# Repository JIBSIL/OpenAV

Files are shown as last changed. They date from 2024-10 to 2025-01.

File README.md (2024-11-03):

## OpenAV

### Important Note

OpenAV is still in beta! Please review the schematic, BOM and PCB to adjust the OpenAV kit to your requirements. It is untested so far, so it may have major bugs and other issues.

### Information
The OpenAV PCB was created to be a universal system for rocketry - with a LoRa long distance radio, a SIM800C for geolocation and Internet communication, an ESP32 for WiFi support and an MPU6050 for sensor data, it provides everything you could want in an avionics system. It integrates seamlessly with the OpenAV library to eliminate coding complexity; with a multitude of ready-to-go configurations, it provides support for any kind of rocket.

This project was created with competitive rocketry in mind, and it therefore utilizes optimized algorithms to provide realtime high-accuracy course predictions, even at supersonic speeds. Uncomplicated and open schematics allow for anyone with basic knowledge to add parts to the system (and if you think other people would like it, make sure to open a pull request on our GitHub for it!)

### Using the Project
Currently we have **not** tested the PCB and software's compatibility, so bugs are likely to occur! As we prepare for our first test flight, we will update this repository with fixes and more clear documentation.

Please see the `pcb/` folder for the KiCad 8.0 files and gerbers.

Please see the `software/` folder for information on the OpenAV software and how to run and connect it.

### Affiliations

This project is part of the [7th PCBWay contest](https://www.pcbway.com/project/shareproject/OpenAV_open_source_software_and_hardware_for_DIY_rocketry_1c6062a0.html). If you'd like to support OpenAV's development, please buy the OpenAV PCB from our PCBWay page!

### Contributing
Contributions are welcome and encouraged! If you have something you would like to add, please open a pull request for it!

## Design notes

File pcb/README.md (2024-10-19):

## OpenAV/pcb

### Information
The gerbers and KiCad 8.0 schematic and PCB files are here. This project will be updated as we evolve to include more sensors and components, and replace old ones. It is functional as it is, and the gerbers are ready to print.

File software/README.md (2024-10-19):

## OpenAV/software

### Running
This project is an example of how you could integrate the library with dummy sensors. You can integrate them directly into the OpenAV PCB sensors using the respective libraries of the sensors. The project as it is, is completely compatible with Wokwi and other simulators. The current state is meant to demonstrate the realtime course recalculation capabilities of the project.

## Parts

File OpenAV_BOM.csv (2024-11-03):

OPENAV BOM | Note: for all suppliers AliExpress is preferred to decrease shipping price, final SUM_PRICE includes minimum quantity of all parts
PART | TYPE | DEALER | PRICE | LINK | DATASHEET | NOTES | SUM_PRICE
Lumberg 2486 01 | USB connector | AliExpress | 1.27 10u | Micro USB 2P 5P Jack Charging Port Plug Dock Charger DIP SMD For Phone Tabletels Speakers etc Port Socket Power Connector - AliExpress 13 | Datasheet for 2486 01 Lumberg USB Connectors | Octopart | micro-04 | 1.27
ESP32-S3-MINI-1-N8 | Main chip | Mouser | 3.1 1u | ESP32-S3-MINI-1U-N8 Espressif Systems | Mouser | mouser.com/datasheet/2/891/esp32_s3_mini_1_mini_1u_datasheet_en-2997643.pdf |  | 3.1
SIMCOM SIM800C | SIM module | AliExpress | 1.9 1u | SIM800C SIM800 Four frequency package Voice SMS data transfer module new original - AliExpress 502 | Datasheet for SIM800C Simcom | Octopart | sketchy | 1.9
SX1278 | LoRa Transciever | AliExpress | 3.26 1u | Ra-01 LoRa SX1278 433M Wireless Spread Spectrum Transmission Module Most Distant 10KM - AliExpress 502 | SX1276-7-8.book |  | 3.26
MPU6050 | Accelerometer | AliExpress | 0.71 1u | 5pcs/lot MPU-6050 MPU6050 MPU-6052C MPU6052C MPU-9150 MPU9150 MPU-9250 MPU9250 MP92 QFN - AliExpress 502 | https://product.tdk.com/system/files/dam/doc/product/sensor/mortion-inertial/imu/data_sheet/mpu-6000-datasheet1.pdf | obsolete on mouser | 0.71
FXMA108BQX | 8 bit digi/analog switcher | Mouser | 0.82 1u | FXMA108BQX onsemi / Fairchild | Mouser | FXMA108 - Dual-Supply, 8-Bit Signal Translator with Configurable Voltage Supplies and Signals Levels, 3-State Outputs and Auto Direction Sensing |  | 0.82
CH340N | USB to serial | AliExpress | 2.28 5u | 5PCS USB To Serial Chip CH340N SOP-8 Built-in Crystal Oscillator - AliExpress 502 | Microsoft Word - CH340.doc |  | 2.28
UFL Molex | Antenna connector | AliExpress | 1.1 20u | 10/20/30PCS High Quality UFL Seat IPEX / IPX Connector U.FL-R-SMT RF Coaxial Connectors Antenna 20279-001E - AliExpress 13 |  |  | 1.1
AMS1117-3v3 | Voltage regulator | AliExpress | 1.08 20u | 50PCS AMS1117 3V3 AMS117-3.3 AMS1117 5.0 AMS1117-5.0 SOT223 Voltage Rugulator - AliExpress | Microsoft Word - DS1117 |  | 1.08
AMS1117-ADJ | Voltage regulator | AliExpress | 1.03 20u | 50pcs AMS1117 3V3 AMS1117-1.2 AMS1117-1.5 AMS1117-1.8 AMS1117-2.5 AMS1117-3.3 AMS1117-5.0 AMS1117-ADJ SOT223 Voltage Rugulator - AliExpress | Microsoft Word - DS1117 |  | 1.03
XT30-UPB | Power connector | AliExpress | 1.65 1u | Original Amass XT30UPB XT30 UPB 2mm Plug Male Female Bullet Connectors Plugs for RC Lipo Battery - AliExpress 26 | n/a |  | 1.65
JAE MicroSIM | microSIM | Ali/Mouser | 7.71 10u/1.22 1u | 10PCS SF53S006VCBR2000 SF72S006VBDR2500 Connectors - AliExpress 502 | n/a | SF53S006VCBR2000 JAE Electronics | Mouser | 1.22
 |  |  |  |  |  |  | 19.42
Resistor | Resistors | Any (AliExpress) |  |  |  | 1k, 2k and 4k resistors needed |  | NOTE: resistors and caps are all size 0603 metric
Capacitor | Capacitor | Any (AliExpress) |  |  |  | 6x 100nF, 2x 300uF, 1x 2.2nF, 1x 22uF

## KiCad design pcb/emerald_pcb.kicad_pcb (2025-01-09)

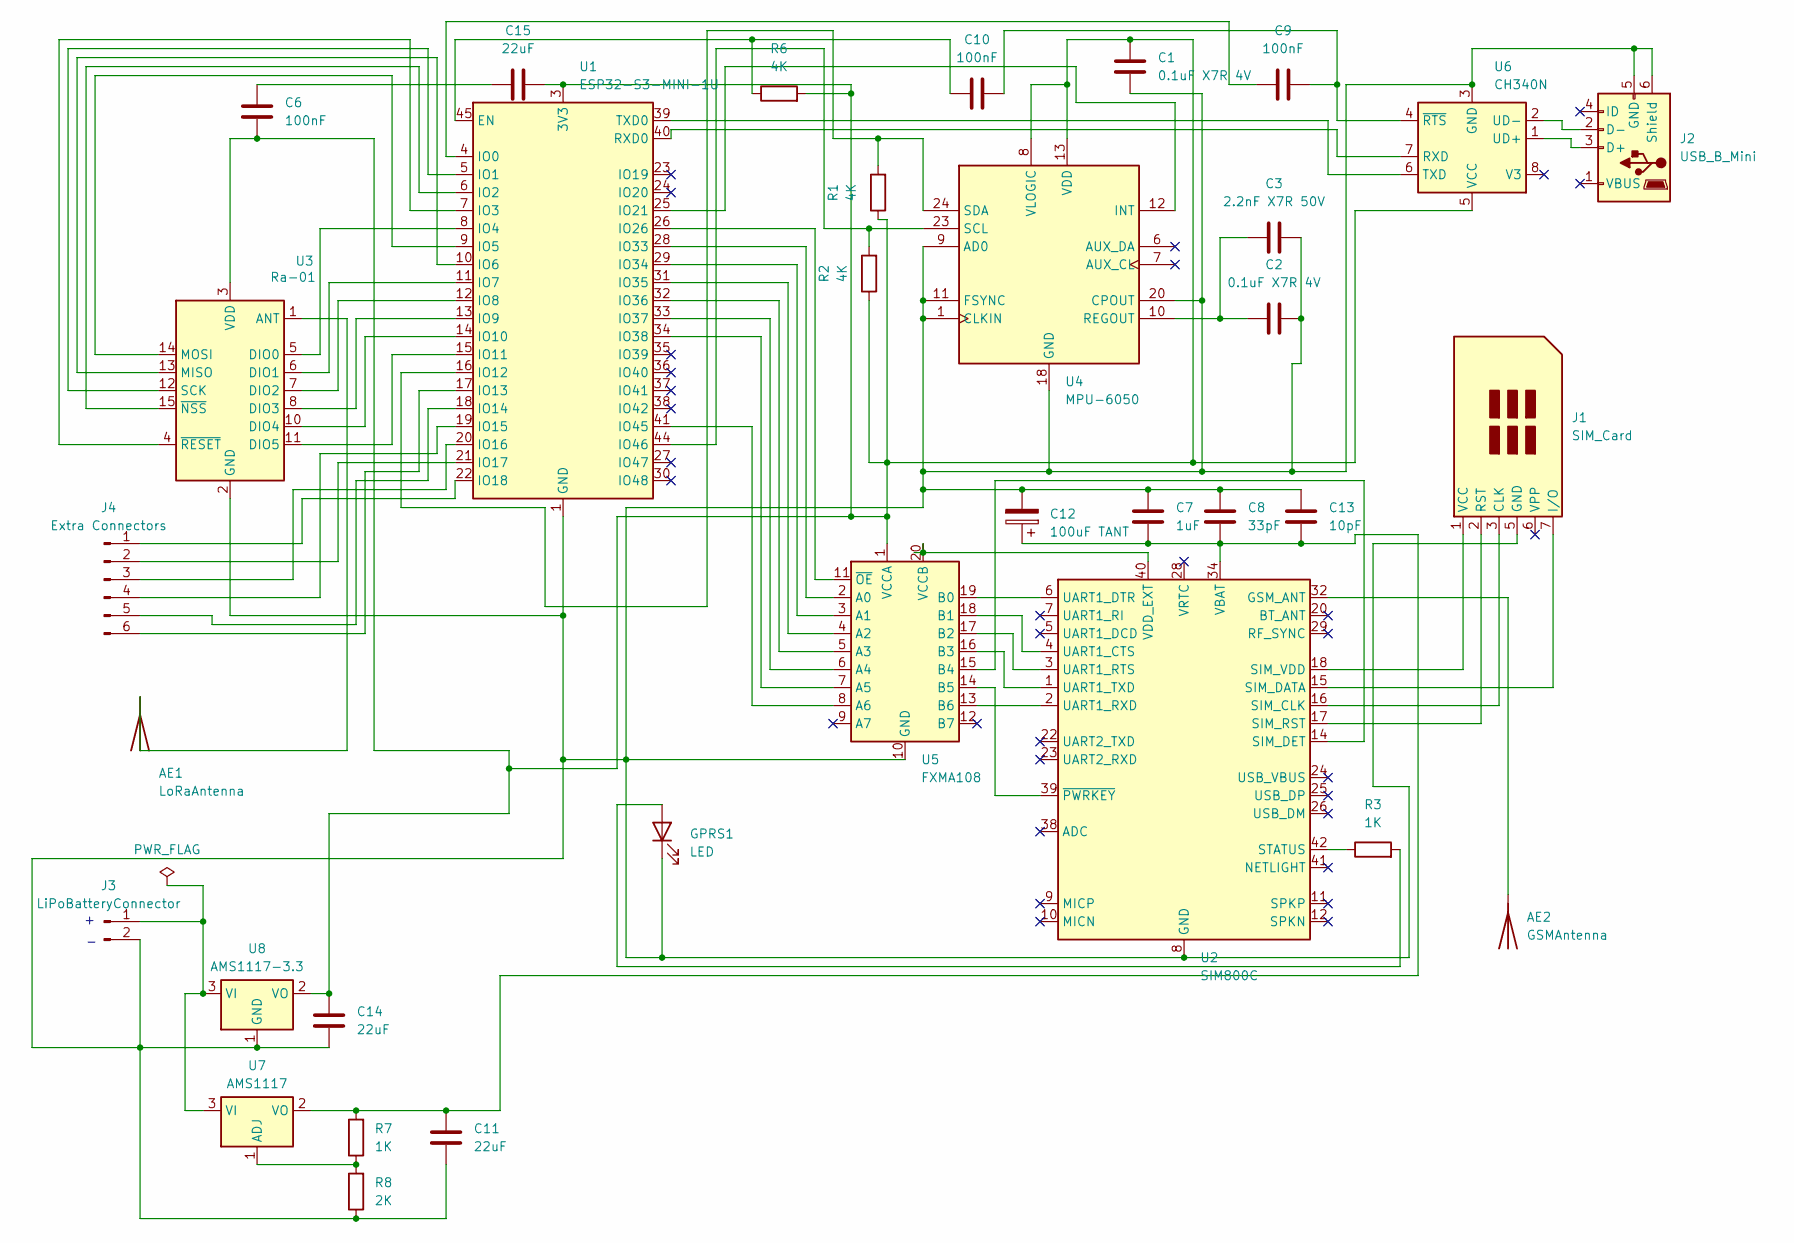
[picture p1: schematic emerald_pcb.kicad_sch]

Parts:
AE1: LoRaAntenna; GB042-34S-H10
AE2: GSMAntenna; GB042-34S-H10
C1, C2: 0.1uF X7R 4V; C_0201_0603Metric
C3: 2.2nF X7R 50V; C_0201_0603Metric
C6, C9, C10: 100nF; C_0201_0603Metric
C7: 1uF; C_0201_0603Metric
C8: 33pF; C_0201_0603Metric
C11, C14, C15: 22uF; C_0201_0603Metric
C12: 100uF TANT; C_0201_0603Metric
C13: 10pF; C_0201_0603Metric
GPRS1: LED; LED_0201_0603Metric
J1: SIM_Card; microSIM_JAE_SF53S006VCBR2000
J2: USB_B_Mini; USB_Mini-B_Lumberg_2486_01_Horizontal
J3: LiPoBatteryConnector; AMASS_XT30U-F_1x02_P5.0mm_Vertical
J4: Extra Connectors; PinHeader_1x06_P1.00mm_Vertical
R1, R2, R6: 4K; R_0201_0603Metric
R3, R7: 1K; R_0201_0603Metric
R8: 2K; R_0201_0603Metric
U1: ESP32-S3-MINI-1U; ESP32-S2-MINI-1U
U2: SIM800C; SIMCom_SIM800C
U3: Ra-01; Ai-Thinker-Ra-01-LoRa
U4: MPU-6050; InvenSense_QFN-24_4x4mm_P0.5mm
U5: FXMA108; WQFN-20-1EP_2.5x4.5mm_P0.5mm_EP1x2.9mm
U6: CH340N; SOP-8_3.9x4.9mm_P1.27mm
U7: AMS1117; SOT-223-3_TabPin2
U8: AMS1117-3.3; SOT-223-3_TabPin2

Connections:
unnamed 1: AE1.1, U3.1 (ANT); also elsewhere on the board
unnamed 2: AE2.1, U2.32 (GSM_ANT); also elsewhere on the board
unnamed: C6.2, C15.1
unnamed: GPRS1.2 (A), R3.2
unnamed: C1.1, C2.2, C3.2, C7.1, C8.1, C11.2, C12.2, C13.1, C14.2, GPRS1.1 (K), J1.5 (GND), J2.5 (GND), J2.6 (Shield), J3.2, R8.1, U1.1 (GND), U1.2 (GND), U1.42 (GND), U1.43 (GND), U1.46 (GND), U1.47 (GND), U1.48 (GND), U1.49 (GND), U1.50 (GND), U1.51 (GND), U1.52 (GND), U1.53 (GND), U1.54 (GND), U1.55 (GND), U1.56 (GND), U1.57 (GND), U1.58 (GND), U1.59 (GND), U1.60 (GND), U1.61 (GND), U1.62 (GND), U1.63 (GND), U1.64 (GND), U1.65 (GND), U2.8 (GND), U2.13 (GND), U2.19 (GND), U2.21 (GND), U2.27 (GND), U2.30 (GND), U2.31 (GND), U2.33 (GND), U2.36 (GND), U2.37 (GND), U3.2 (GND), U3.9 (GND), U3.16 (GND), U4.1 (CLKIN), U4.9 (AD0), U4.11 (FSYNC), U4.18 (GND), U4.20 (CPOUT), U5.10 (GND), U6.3 (GND), U8.1 (GND)
unnamed: J1.3 (CLK), U2.16 (SIM_CLK)
unnamed: J1.7 (I/O), U2.15 (SIM_DATA)
unnamed: J1.2 (RST), U2.17 (SIM_RST)
unnamed: J1.1 (VCC), U2.18 (SIM_VDD)
unnamed: J2.3 (D+), U6.1 (UD+)
unnamed: J2.2 (D-), U6.2 (UD-)
unnamed 12: J3.1, U7.3 (VI), U8.3 (VI); also elsewhere on the board
unnamed: J4.1, U1.22 (IO18)
unnamed: J4.2, U1.21 (IO17)
unnamed: J4.3, U1.20 (IO16)
unnamed: J4.4, U1.19 (IO15)
unnamed: J4.5, U1.18 (IO14)
unnamed: J4.6, U1.17 (IO13)
unnamed 19: C1.2, C6.1, C14.1, C15.2, R1.1, R2.1, R6.2, U1.3 (3V3), U3.3 (VDD), U4.8 (VLOGIC), U4.13 (VDD), U5.1 (VCCA), U6.5 (VCC), U8.2 (VO); also elsewhere on the board
unnamed: C10.1, R6.1, U1.45 (EN)
unnamed: C9.1, U1.4 (IO0)
unnamed: U1.5 (IO1), U3.12 (SCK)
unnamed: U1.6 (IO2), U3.15 (~NSS)
unnamed: U1.7 (IO3), U3.4 (~RESET)
unnamed: U1.8 (IO4), U3.5 (DIO0)
unnamed: U1.9 (IO5), U3.14 (MOSI)
unnamed: U1.10 (IO6), U3.13 (MISO)
unnamed: U1.11 (IO7), U3.6 (DIO1)
unnamed: U1.12 (IO8), U3.7 (DIO2)
unnamed: U1.13 (IO9), U3.8 (DIO3)
unnamed: U1.14 (IO10), U3.10 (DIO4)
unnamed: U1.15 (IO11), U3.11 (DIO5)
unnamed: R1.2, U1.16 (IO12), U4.24 (SDA)
unnamed: U1.25 (IO21), U4.12 (INT)
unnamed: U1.26 (IO26), U5.11 (~OE)
unnamed: U1.28 (IO33), U5.2 (A0)
unnamed: U1.29 (IO34), U5.3 (A1)
unnamed: U1.31 (IO35), U5.4 (A2)
unnamed: U1.32 (IO36), U5.5 (A3)
unnamed: U1.33 (IO37), U5.6 (A4)
unnamed: U1.34 (IO38), U5.7 (A5)
unnamed: U1.41 (IO45), U5.8 (A6)
unnamed: R2.2, U1.44 (IO46), U4.23 (SCL)
unnamed: U1.40 (RXD0), U6.7 (RXD)
unnamed: U1.39 (TXD0), U6.6 (TXD)
unnamed: U2.14 (SIM_DET), U5.15 (B4)
unnamed: R3.1, U2.42 (STATUS)
unnamed: U2.4 (UART1_CTS), U5.18 (B1)
unnamed: U2.6 (UART1_DTR), U5.19 (B0)
unnamed: U2.3 (UART1_RTS), U5.17 (B2)
unnamed: U2.2 (UART1_RXD), U5.13 (B6)
unnamed: U2.1 (UART1_TXD), U5.16 (B3)
unnamed: U2.40 (VDD_EXT), U5.20 (VCCB)
unnamed: U2.39 (~PWRKEY), U5.14 (B5)
unnamed: C2.1, C3.1, U4.10 (REGOUT)
unnamed: C9.2, C10.2, U6.4 (~RTS)
unnamed: R7.1, R8.2, U7.1 (ADJ)
unnamed: C7.2, C8.2, C11.1, C12.1, C13.2, R7.2, U2.34 (VBAT), U2.35 (VBAT), U7.2 (VO)

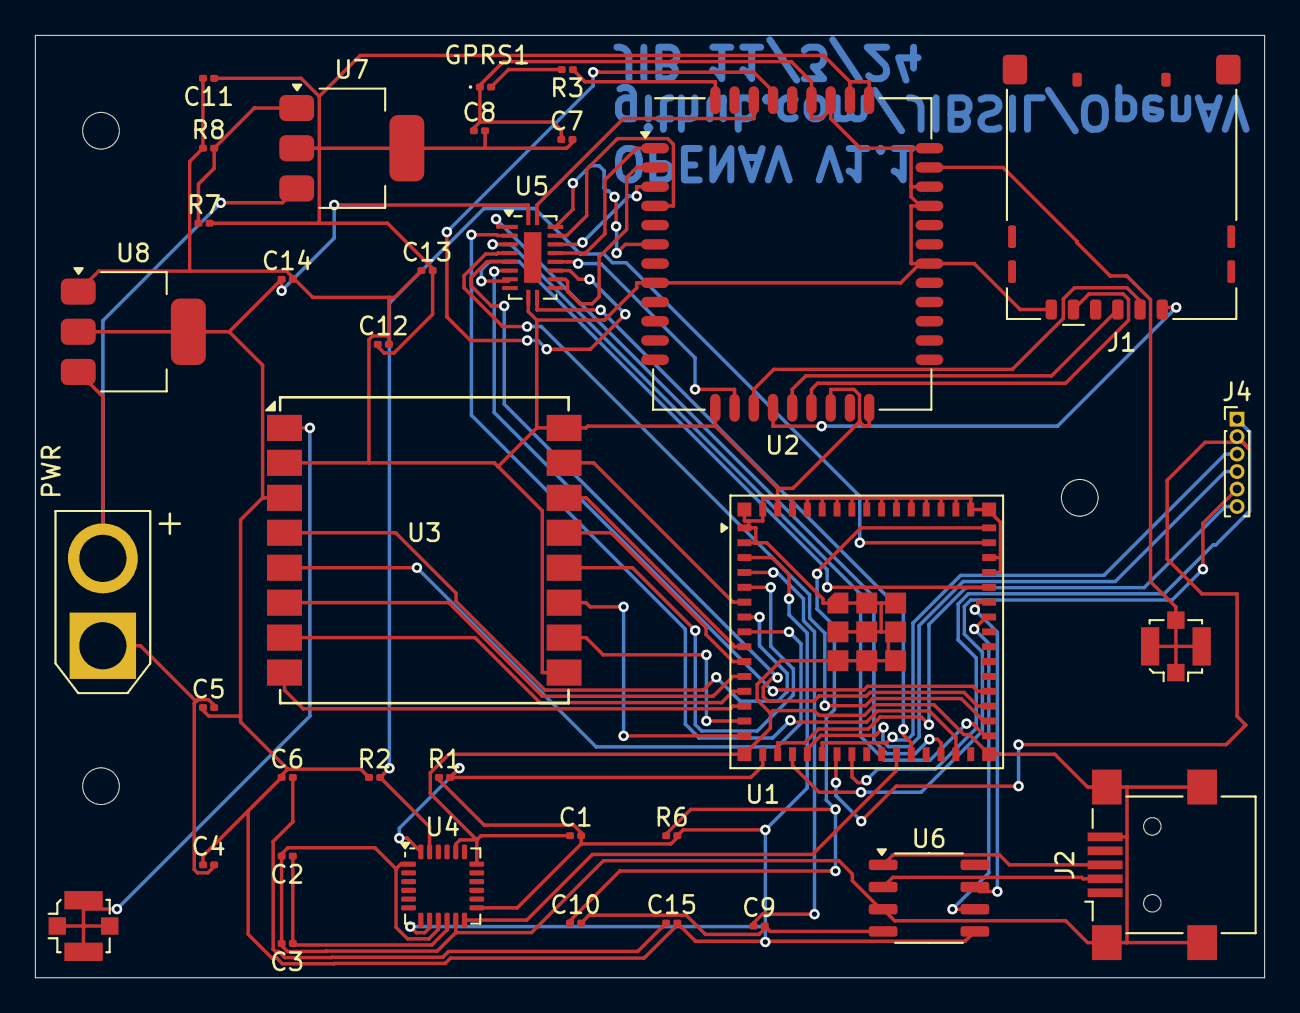
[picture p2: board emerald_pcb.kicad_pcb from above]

Board: 2 copper layers, 70.3 x 53.9 mm, 39 parts (0 on the bottom side), 59 nets.

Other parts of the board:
ANT1: LoRaAnt; U.FL_Molex_MCRF_73412-0110_Vertical
ANT2: GSMConn; U.FL_Molex_MCRF_73412-0110_Vertical
C4, C5: 100nF; C_0201_0603Metric
PWR: AMASS_XT30U-F_1x02_P5.0mm_Vertical
S1, S2, S3: MountingHole_2.1mm

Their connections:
unnamed: C4.2, C5.2, PWR.1
unnamed 1: ANT1.1, ANT1.2; also elsewhere on the board
unnamed 2: ANT2.1, ANT2.2; also elsewhere on the board
unnamed 12: PWR.2; also elsewhere on the board
unnamed 19: C4.1, C5.1; also elsewhere on the board

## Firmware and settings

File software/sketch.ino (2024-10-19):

#include "SatNav.h"
#include "StageManager.h"
#include "VectorMath.h"

#define PIN_TRIG 12
#define PIN_ECHO 11
#define PIN_LAUNCH 10
#define PIN_IGNITION 9
#define DEBUG_ULTRASONIC_NO_OUTPUT_FOUND_LOW 390
#define DEBUG_ULTRASONIC_NO_OUTPUT_FOUND_HI 410
//#define USE_ALTERNATIVE_ACCURATE_SEEKING true

// drag
const float ROCKET_CROSS_SECTIONAL_AREA_M = 0.2;

Stage stage = StageManager().stage;
SatNav satNav = SatNav(stage);
VectorMath vectorMath = VectorMath(satNav, ROCKET_CROSS_SECTIONAL_AREA_M);

bool ignitionTrigger = false;
bool launched = false;

int getUltrasonicDistance() {
  digitalWrite(PIN_TRIG, HIGH);
  delayMicroseconds(10);
  digitalWrite(PIN_TRIG, LOW);

  int duration = pulseIn(PIN_ECHO, HIGH);
  return duration / 58;
}

void launchSequence() {
  Serial.println(F("[LAUNCH] Starting countdown"));
  Serial.println(F("[LAUNCH] Launch in 10"));
  delay(1000);
  // on each print statement, broadcast on LoRa frequency
  Serial.println(F("[LAUNCH] Launch in 9"));
  delay(1000);
  Serial.println(F("[LAUNCH] Launch in 8"));
  delay(1000);
  Serial.println(F("[LAUNCH] Launch in 7"));
  delay(1000);
  Serial.println(F("[LAUNCH] Launch in 6"));
  delay(1000);
  Serial.println(F("[LAUNCH] Launch in 5"));
  delay(1000);
  digitalWrite(PIN_IGNITION, HIGH);
  Serial.println(F("[LAUNCH] Launch in 4"));
  delay(1000);
  Serial.println(F("[LAUNCH] Launch in 3"));
  delay(1000);
  Serial.println(F("[LAUNCH] Launch in 2"));
  delay(1000);
  Serial.println(F("[LAUNCH] Launch in 1"));
  delay(1000);
  
}

void setup() {
  Serial.begin(74800, SERIAL_8N1);
  pinMode(PIN_TRIG, OUTPUT);
  pinMode(PIN_ECHO, INPUT);
  pinMode(PIN_LAUNCH, INPUT_PULLUP);
  pinMode(PIN_IGNITION, OUTPUT);
  stage = Stage::WAIT;
  Serial.println(F("Emerald I onboard computer initialized!"));

  float x, z;
  unsigned long millis_start = millis();
  #if USE_ALTERNATIVE_ACCURATE_SEEKING
  vectorMath.alternative_seeking(x, z);
  #else
  vectorMath.original_optimize(x, z);
  #endif
  Serial.println("[LAUNCH HELPER] Optimal launch angle found in " + String((millis() - millis_start) / 1000.0) + "s! X: " + String(x) + ", Z: " + String(z));
}

void loop() {
  int buttonValue = digitalRead(PIN_LAUNCH);

  if(buttonValue != HIGH) {
    ignitionTrigger = true;
  }

  if(ignitionTrigger && !launched) {
    stage = Stage::IGNITION;
    ignitionTrigger = false;
    int dist = getUltrasonicDistance();
    if(dist > DEBUG_ULTRASONIC_NO_OUTPUT_FOUND_LOW && dist < DEBUG_ULTRASONIC_NO_OUTPUT_FOUND_HI) {
      Serial.println(F("[LAUNCH HELPER] Rocket successfully changed to IGNITION stage!"));
      stage = Stage::IGNITION;
      launched = true;
      launchSequence();
    } else {
      Serial.println("[LAUNCH HELPER] Launch is unsafe! Rocket is pointing at an object " + String(dist) + "cm away");
    }
  }
  delay(50);
}

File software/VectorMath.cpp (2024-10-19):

#include "VectorMath.h" 

#define distanceDebug false

const float rocketMass = 0.5;
const float defaultSeaLevelAirDensity = 1.225;
const int num_points = 18;

float _rocketArea;
float sea_level_temp = 15.0;
float sea_level_humidity = 60.0;

// air density calculation constants
const float p0 = 101325; // Sea level standard pressure (Pa)
const float T0 = 288.15; // Sea level standard temperature (K)
const float L = 0.0065; // Temperature lapse rate (K/m)
const float R = 287.05; // Specific gas constant for dry air (J/kg/K)
const float g = 9.80665; // Gravitational acceleration (m/s^2)
const float M = 0.0289644; // Molar mass of Earth's air (kg/mol)

// humidity calculation constants
// ONLY accurate up to 2-3km
const float H_humid = 2500.0;

// temperature calculation constant with alt
// only works up to 11km
const float lapse_rate = 0.0065;

float thrust_time[num_points] = {
  0.000, 0.005, 0.046, 0.059, 0.100, 0.200, 0.400, 0.500, 0.600, 0.796, 0.894, 0.951, 
  0.964, 1.000, 1.052, 1.106, 1.144, 1.180
};

// this will be filled by the launch helper
float time_squared_table[num_points];
float precomputed_density[50];

float thrust_force[num_points] = {
  0.000, 40.438, 817.754, 813.261, 772.822, 736.877, 696.439, 669.480, 620.055, 
  539.178, 485.261, 453.809, 435.836, 274.082, 152.767, 62.904, 13.480, 0.000
};

float calculate_air_density(float altitude, float temperature, float humidity) {  
  float T = temperature + 273.15;

  // pressure at altitude
  float pressure = p0 * pow((1 - (L * altitude) / T0), (g * M) / (R * L));
  float es = 6.1078 * pow(10.0, (7.5 * temperature) / (temperature + 237.3)) * 100; // convert hPa to Pa
  float e = humidity * es;
  float r = 0.622 * (e / (pressure - e));
  float Tv = T * (1 + 0.61 * r);
  float air_density = pressure / (R * Tv);
  return air_density;
}

// simple exponential decay
float calculate_humidity_at_altitude(float sea_level_humidity, float altitude) {
  float humidity_at_altitude = sea_level_humidity * exp(-altitude / H_humid);
  if (humidity_at_altitude < 0) {
    humidity_at_altitude = 0;
  }
  return humidity_at_altitude;
}

// linear
float calculate_temperature_at_altitude(float sea_level_temperature, float altitude) {
  float temperature_at_altitude = sea_level_temperature - (lapse_rate * altitude);
  return temperature_at_altitude;
}

// basic noncomputed drag curve for max speed
float drag_coeff(float mach_number) {
  float drag_coefficient;
  if (mach_number < 0.8) {
      drag_coefficient = 0.3;
  } else if (mach_number < 1.0) {
      drag_coefficient = 0.5;
  } else if (mach_number < 1.5) {
      drag_coefficient = 0.8;
  } else {
      drag_coefficient = 1.0;
  }
  return drag_coefficient;
}

VectorMath::VectorMath(SatNav& sn, float rocketArea) {
  _satnav = sn;
  _rocketArea = rocketArea;

  Serial.println("Preloading density...");
  for(int i = 0; i < 50; i++) {
    float dy = 75 * i;
    float temp = calculate_temperature_at_altitude(sea_level_temp, dy);
    float humidity = calculate_humidity_at_altitude(sea_level_humidity, dy);

    float airDensity = calculate_air_density(dy, temp, humidity);
    precomputed_density[i] = airDensity;
  }
}

// this is used to calculate "n" coordinate distance (notation uses X direction for clarity)
void calculate_n_distance_from_origin(int angleX, float &dx) {
  float vx = 0;

  float cosXMass = cos(DEGREE_RAD_CONVERSION * float(angleX)) / rocketMass;

  for(int i = 1; i < num_points; i++) {
    float accelX = cosXMass * thrust_force[i];
    float dragCoeff = drag_coeff(vx / 343.0);

    float temp = calculate_temperature_at_altitude(sea_level_temp, dx);
    float humidity = calculate_humidity_at_altitude(sea_level_humidity, dx);

    float airDensity = calculate_air_density(dx, temp, humidity);
    float drag_force = 0.5 * dragCoeff * airDensity * _rocketArea * vx * vx;

    // vf^2=vi^2+2ad
    dx = (vx * thrust_time[i]) + (0.5 * accelX * time_squared_table[i]);

    vx += sqrt(2.0 * accelX * dx);
    
    // test for nan
    if(vx != vx) {
      vx = 0;
    }
  }
}

float signum(float x) {
  if (x > 0.0f) return 1;
  if (x < 0.0f) return -1;
  return 0;
}

// this is used to calculate "n" coordinate distance (notation uses X direction for clarity)
void calculate_supersonic_n_distance_from_origin(int angleX, float &dx, float &maxdzy) {
  float vx = 0.0f, vy = 0.0f, dy = 0.0f;

  float cosX = cos(DEGREE_RAD_CONVERSION * float(angleX));
  float sinX = sin(DEGREE_RAD_CONVERSION * float(angleX));

  for(int i = 1; i < num_points; i++) {
    float timestep = thrust_time[i] - thrust_time[i - 1];
    float dt2 = timestep * timestep;
    float dragCoeff = drag_coeff(vy / 343.0);
    
    float vel = sqrt((vx * vx) + (vy * vy));
    float airDensity = precomputed_density[(int) floor(dy / 75)];
    float drag_force = 0.5 * dragCoeff * airDensity * _rocketArea * vel * vel;

    float fY = thrust_force[i] * sinX;
    float fX = thrust_force[i] * cosX;

    float dragY = drag_force * sinX * (signum(fY) * -1);
    float dragX = drag_force * cosX * (signum(fX) * -1);

    float accelY = (fY - g + dragY) / rocketMass;
    float accelX = (fX + drag_force) / rocketMass;

    if(dy > maxdzy) {
      maxdzy = dy;
    }

    //vx = sqrt((vx * vx) + (2.0 * accelX * dx));
    //vy = sqrt((vy * vy) + (2.0 * accelY * dy));
    vx += accelX * timestep;
    vy += accelY * timestep;

    // vf^2=vi^2+2ad
    // d=vit + 1/2at^2
    dx += (vx * timestep) + (0.5 * accelX * dt2);
    dy += (vy * timestep) + (0.5 * accelY * dt2);

    if(distanceDebug) {
      Serial.println("");
      Serial.println("AngleX " + String(angleX));
      Serial.println("DragCoeff " + String(dragCoeff));
      Serial.println("Vel " + String(vel));
      Serial.println("AirDensity " + String(airDensity));
      Serial.println("DragForce " + String(drag_force));
      Serial.println("SinX " + String(sinX));
      Serial.println("ThrustForce " + String(thrust_force[i]));
      Serial.println("AccelY " + String(accelY));
      Serial.println("fY " + String(fY));
      Serial.println("fX " + String(fX));
      Serial.println("CosX " + String(cosX));
      Serial.println("AccelX " + String(accelX));
      Serial.println("Dx " + String(dx));
      Serial.println("Dy " + String(dy));
    }
    
    // test for nan
    if(vx != vx) {
      vx = 0;
    }

    if(vy != vy) {
      vy = 0;
    }
  }
}
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

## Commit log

2024-10-19 feat: initial commit of PCB and software
    [emerald_pcb.kicad_pcb, emerald_pcb.kicad_sch]
2024-10-19 feat: add gerbers to PCB folder
    [emerald_pcb-B_Adhesive.gbr, emerald_pcb-B_Courtyard.gbr, emerald_pcb-B_Cu.gbr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]
2024-10-19 feat: add readme for pcb and software folders
2024-11-03 feat: update to version 1.1
    Changed power inputs, various schematic changes, added decoupling capacitors, removed rare components
    [emerald_pcb-B_Adhesive.gbr, emerald_pcb-B_Courtyard.gbr, emerald_pcb-B_Cu.gbr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]
2024-11-03 feat: add BOM and IBOM for v1.1
    [OpenAV_BOM.csv]
2025-01-09 feat: added pins to schem. fix: D+ and D- pins being assigned on ESP32
    [emerald_pcb.kicad_pcb, emerald_pcb.kicad_sch]
2025-01-09 feat: reroute for fewer vias, simplify design
    [emerald_pcb.kicad_pcb, emerald_pcb.kicad_sch]
